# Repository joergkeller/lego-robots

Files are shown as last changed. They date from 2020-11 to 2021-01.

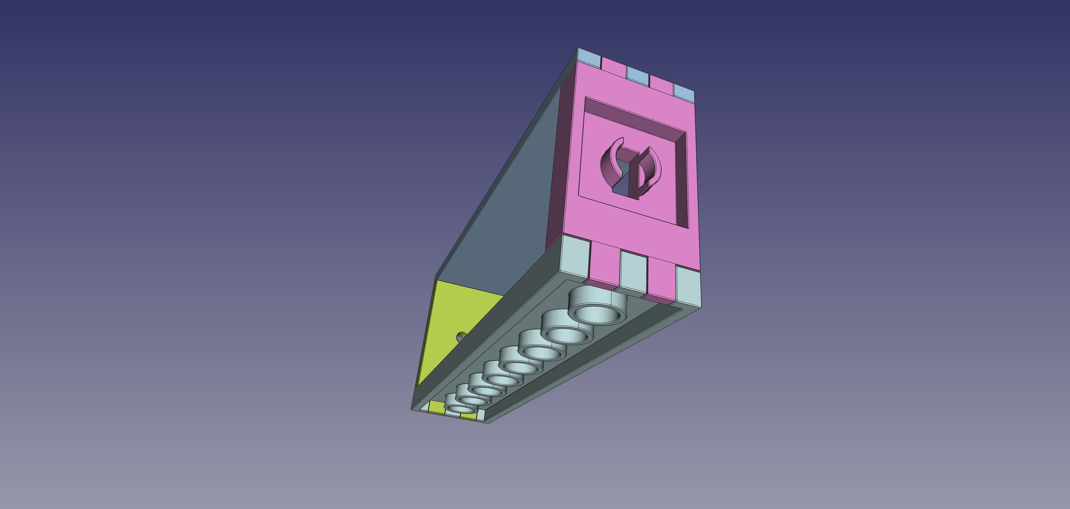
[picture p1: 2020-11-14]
3dp/gearbox-tt-motor/images/motor-case-bottom.png

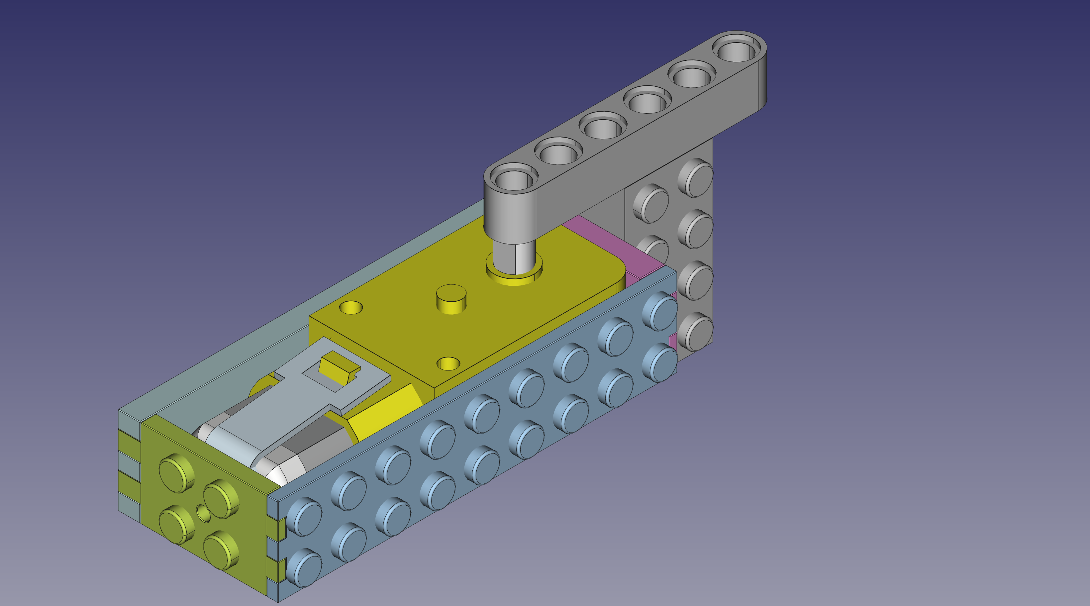
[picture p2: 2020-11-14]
3dp/gearbox-tt-motor/images/motor-case-technic.png

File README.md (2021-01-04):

# Lego Roboter
Adapter-Platten und Code für Lego Roboter mit Arduino.

## 3D-Prints
* Lego-Adapter für Gearbox TT DC Motor
* Case für Sparkfun Qwiik Motor Driver

## Control Code
* Control 2 motors with Joystick using Adafruit QT Py (M0)

# Ideen

## Controller
* [Metro ESP32-S2](https://www.adafruit.com/product/4775): ESP32-S2, Uno, Qwiic, LiPo, max. 12V Input
* [TTGO T7 Mini32](http://www.lilygo.cn/prod_view.aspx?TypeId=50033&Id=978&FId=t3:50033:3): ESP32, Qwiic, LiPo, 
* [Beetle ESP32](https://www.dfrobot.com/product-1798.html): ESP32, 4x Digital, 4x Analog, I2C, 5V Input
* [QT Py](https://www.adafruit.com/product/4600): M0, Qwiic, 5V Input

## Motor Driver
* [Qwiic Motor Driver](https://www.sparkfun.com/products/15451): 2x DC Motor, I2C, 6-12V, 1.2-1.5A
* [Arduino Motor/Stepper/Servo Shield](https://www.adafruit.com/product/1438): 4x Motor oder 2x Stepper, 2x Servo, I2C, 4.5-13.5V, 1.2-2.0A
* [Motor/Stepper Feather Wing](https://www.adafruit.com/product/2927): 4x Motor oder 2x Stepper, I2C, 4.5-13.5V, 1.2A

## Proximity
* [Qwiic Proximity/Gesture/Light/RGB](https://www.adafruit.com/product/3595)

## Joystick
* [Analog ohne Switch](https://www.adafruit.com/product/444): 19x19x9 mm
* [Analog mit Switch](https://www.adafruit.com/product/512): 38x38x32 mm
* [Analog mit Switch](https://www.sparkfun.com/products/9032): 26x32x35 mm
* [I2C, Analog mit Switch](https://www.sparkfun.com/products/15168)

## Diverses
* [Qwiic Differential I2C](https://www.sparkfun.com/products/14589): z.B. Kabelfernsteuerung
* [Qwiic Rotary Encoder](https://www.sparkfun.com/products/15083)
* [I2C Port Expander In/Out, Key driver](https://www.sparkfun.com/products/13601)

Further
* https://maker.pro/arduino/projects/how-to-control-an-arduino-robot-with-a-ps4-bluetooth-controller
* https://techtutorialsx.com/2020/02/16/esp32-connecting-a-ps3-controller/

# Bestellungen

| Komponente | Nr. | Bastelgarage | Mouser | Digikey |
| --- | --- | --- | --- | --- |
| Qwiic Motor Driver | ROB-15451 | - | 15.- [474-ROB-15451](https://www.mouser.ch/ProductDetail/474-ROB-15451) | 14.- [ROB-15451](https://www.digikey.ch/products/de?keywords=ROB-15451) | 
| Qwiic Joystick | COM-15168 | - | - | 9.- [COM-15168](https://www.digikey.ch/products/de?keywords=COM-15168)
| Qwiic Cable 100mm | [4210](https://www.adafruit.com/product/4210) | | | 0.85 [1528-4210-ND](https://www.digikey.ch/product-detail/de/4210/1528-4210-ND/10230021/?itemSeq=347876058)
| Beetle ESP32 (Mini) | [SKU:DFR0575](https://www.dfrobot.com/product-1798.html) | 17.- [Beetle ESP32](https://www.bastelgarage.ch/beetle-esp32-mikrocontroller) | 13.- [426-DFR0575](https://www.mouser.de/ProductDetail/DFRobot/DFR0575?qs=0lSvoLzn4L%252Bs0iCsotbjvQ%3D%3D) | (15.- [DFR0575-ND](https://www.digikey.com/en/products/detail/dfrobot/DFR0575/9805793?s=N4IgTCBcDaICIDEBKAGArAdjSAugXyA)) |
| TTGO T7 Mini32 v1.4 | [T7 Mini32](http://www.lilygo.cn/prod_view.aspx?TypeId=50033&Id=978&FId=t3:50033:3) ($10) | - | - | - | 
| Adafruit QT Py | [4600](https://www.adafruit.com/product/4600) | - | (6.- [485-4600](https://www.mouser.ch/ProductDetail/Adafruit/4600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)) | (6.- [1528-4600-ND](https://www.digikey.ch/products/de?keywords=adafruit%204600)) |
| Adafruit Feather S2 | [4769](https://www.adafruit.com/product/4769) | - | (21.- [485-4769](https://www.mouser.ch/ProductDetail/Adafruit/4769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)) | (20.- [1528-4769-ND](https://www.digikey.ch/products/de?keywords=adafruit%204769))  |
| Batteriehalter 4x AA | | | | 1.80 [Snap no switch](https://www.digikey.ch/product-detail/de/mpd-memory-protection-devices/BC4AASF/BC4AASF-ND/2439259)
| Batteriehalter 6x AA | [248](https://www.adafruit.com/product/248) | | 
| Batteriehalter 8x AA | [875](https://www.adafruit.com/product/875) | - | 5.50 [485-875](https://www.mouser.ch/ProductDetail/Adafruit/875?qs=%2Fha2pyFaduizQR4J0KLqUOCJvC8o7PvfVDMcjxi9FxQ%3D) | 5.40 [1528-1165-ND](https://www.digikey.ch/product-detail/de/adafruit-industries-llc/875/1528-1165-ND/5353625) <br/> 2.70 [Snap no switch](https://www.digikey.ch/product-detail/de/mpd-memory-protection-devices/BH48AASF/BH48AASF-ND/1951883)
| DC-Jack 2.1/5.5mm | | | 1.- [163-1060-EX](https://www.mouser.ch/ProductDetail/Kobiconn/163-1060-EX?qs=%2Fha2pyFaduiKOJdLWmEw0r8MjDVUk%2FgXSdyB8vAjlO0%3D) | 1.50 [486-3380-ND](https://www.digikey.ch/product-detail/de/schurter-inc/4840-2200/486-3380-ND/1212406)
| Pushbutton |
| 2x Sparkfun Joystick | [COM-09032](https://www.sparkfun.com/products/9032) | | 3.60 [474-COM-09032](https://www.mouser.ch/ProductDetail/SparkFun/COM-09032?qs=WyAARYrbSnb9u7eU4VaEfQ%3D%3D) | 3.60 [1568-1526-ND](https://www.digikey.ch/product-detail/de/sparkfun-electronics/COM-09032/1568-1526-ND/6823623)
| Rotary Encoder/Switch | | | | 3.20 [6mm abgeflacht](https://www.digikey.ch/product-detail/de/cui-devices/ACZ11BR4E-15FD1-20C/102-1769-ND/1923364)
| 2x Multihub Wheel | [4205](https://www.adafruit.com/product/4205)| | | 1.95 [1528-2964-ND](https://www.digikey.ch/products/de?keywords=adafruit%204205)
| Gearmotor 105rpm 6V | [FIT0484](https://www.dfrobot.com/product-1434.html) | | | 11.- [FIT0484](https://www.digikey.ch/product-detail/de/dfrobot/FIT0484/1738-1264-ND/7087161)

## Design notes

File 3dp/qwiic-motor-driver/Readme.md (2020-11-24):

# I2C-gesteuerter Motor Treiber

[Sparkfun Qwiic Motor Driver](https://www.sparkfun.com/products/15451)
* 2x DC Motor
* I2C (Qwiic)
* 3.3V VCC und Logik, 6-12V, 1.2A steady state, max. 1.5A pro Kanal

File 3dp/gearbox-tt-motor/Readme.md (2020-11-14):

# Gearbox TT DC Motor

https://www.bastelgarage.ch/bauteile/stepper-motoren/dc-motoren/getriebemotor-1-48

https://www.adafruit.com/product/3777

## 3D-Print Adapter
Die 4 Lego-Adapter können jeweils passend angeordnet gedruckt werden. Meine beiden Prototypen wurden mit ABS gedruckt, 0.2 mm Düse, 0.1 mm Layer, Nachbearbeitung mit Feile und Drahtbürste.

Die 4 Teile wurden bündig um den Motor eingepasst, der Nippel beim Getriebe und die Achse beim Motor passen bündig in die Stirnseiten, die beiden anderen Teile können verzahnt verbunden werden (evtl. mit Schleifpapier nachbessern). Mit Weissleim oder Sekundenkleber verkleben. Ich habe mit Legosteinen einen Halter gebaut um die richtige Ausrichtung beim Trocknen sicherzustellen.

## Technische Details
* Betriebsspannung: 3V bis 6V DC
* Stromaufnahme: max ca. 250mA
* Torque: max. 0.8kg/cm
* Getriebe Verhältnis: 1:48
* Geschwindigkeit: ca. 26 RPM bei 3V, 44RPM bei 5V
* Abmessung: 69 x 22.5 x 36.5mm
* Gewicht: 27g

## 3D-Model
https://grabcad.com/library/dc-3v-6v-tt-motor-1

## Zubehör
* [68 mm Rad](https://www.adafruit.com/product/3763)
* [65 mm Lego-Rad mit Adapter](https://www.adafruit.com/product/4205)
* [Lego-Adapter](https://www.adafruit.com/product/3810)
* [Adapter](https://www.adafruit.com/product/3769)
* [Encoder-Scheibe](https://www.adafruit.com/product/3782)

## Alternative
* [TT-Motor Metall](https://www.adafruit.com/product/3801)
* [TT-Motor mit Encoder](https://www.sparkfun.com/products/16413)
* [N20 Motor mit Encoder](https://www.adafruit.com/product/4639)
* [Mini Stepper Motor](https://www.adafruit.com/product/4411)

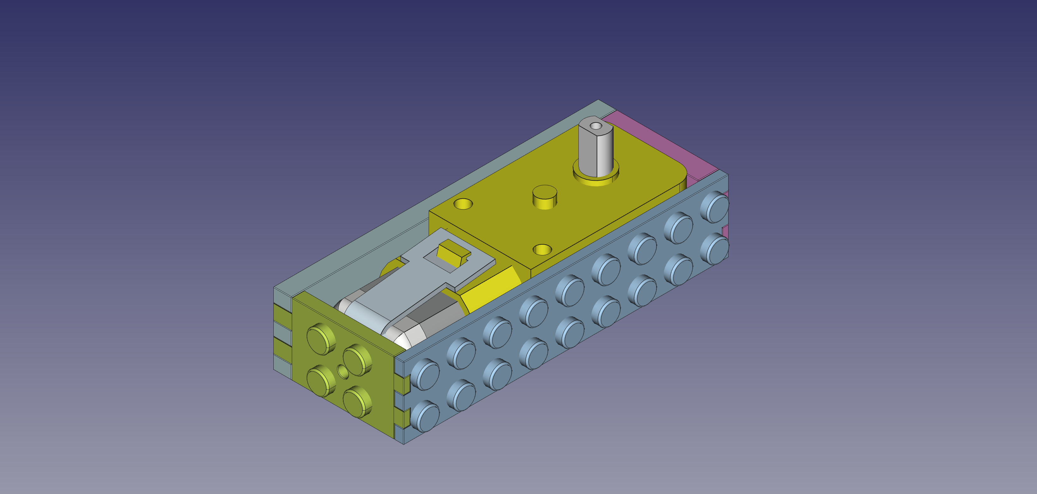
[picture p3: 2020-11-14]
3dp/gearbox-tt-motor/images/motor-case-with-gearbox-tt.png

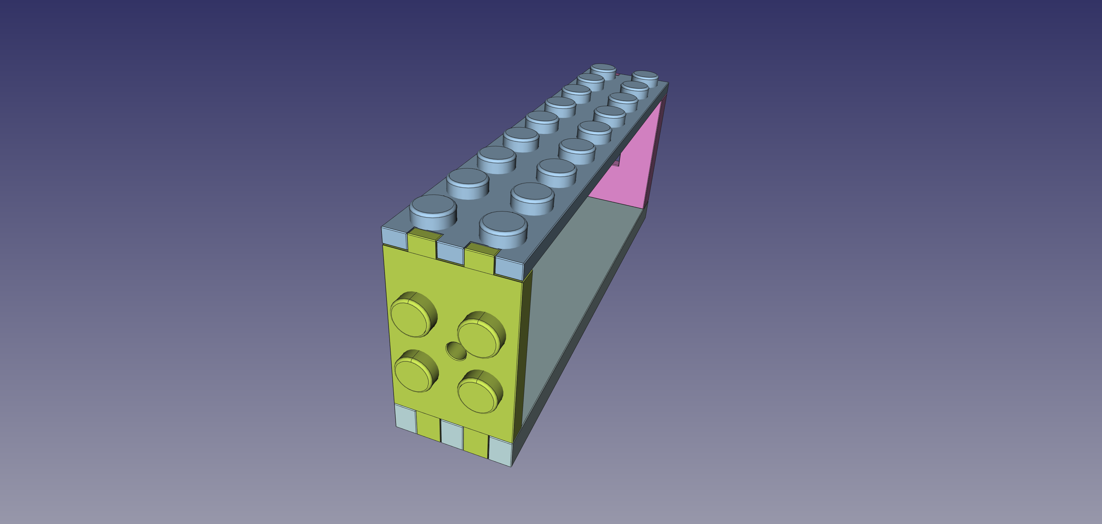
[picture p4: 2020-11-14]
3dp/gearbox-tt-motor/images/motor-case-top.png

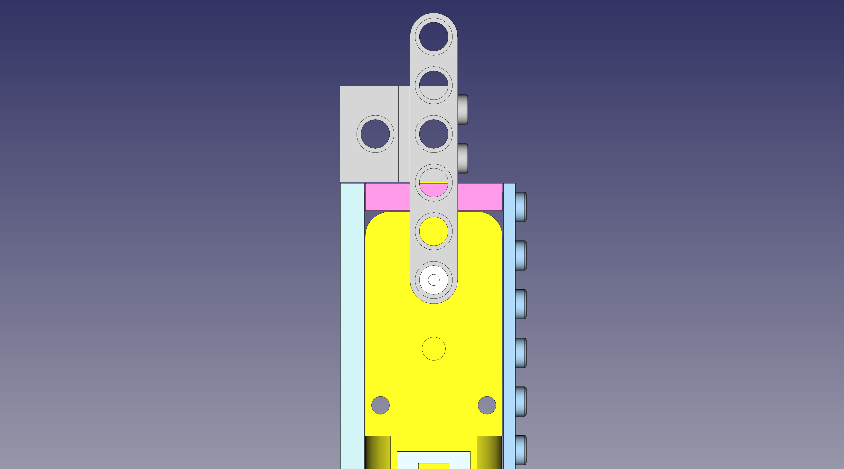
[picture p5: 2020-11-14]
3dp/gearbox-tt-motor/images/motor-case-technic-aligned.png

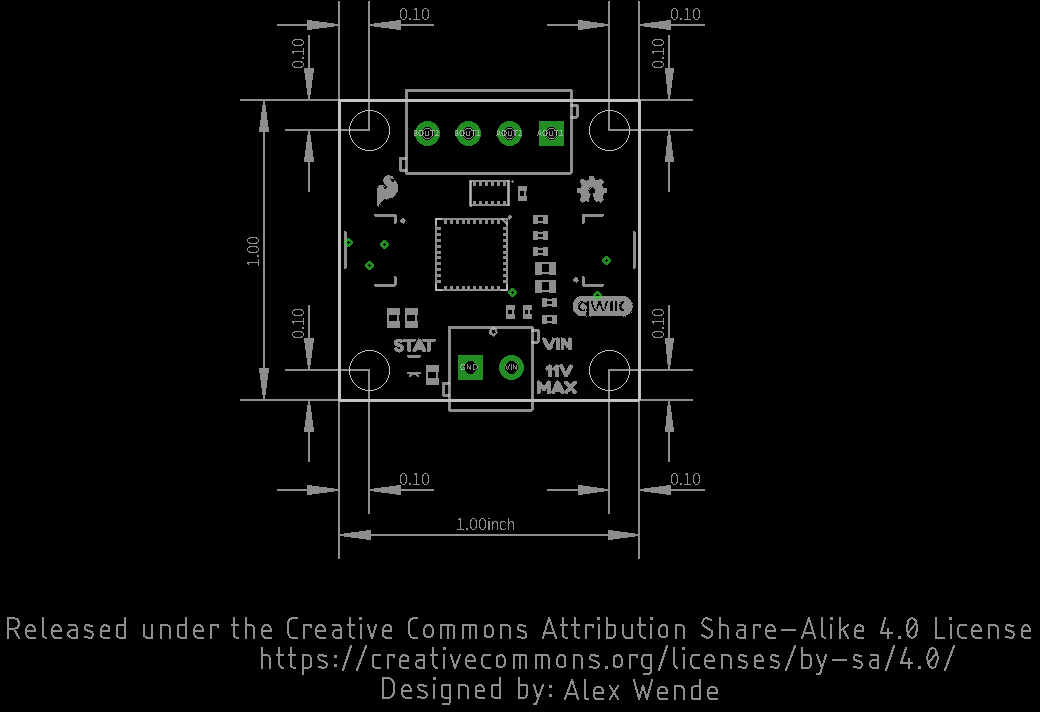
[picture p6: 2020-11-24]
3dp/qwiic-motor-driver/images/Qwiic_Motor_driver_Dimensions.png

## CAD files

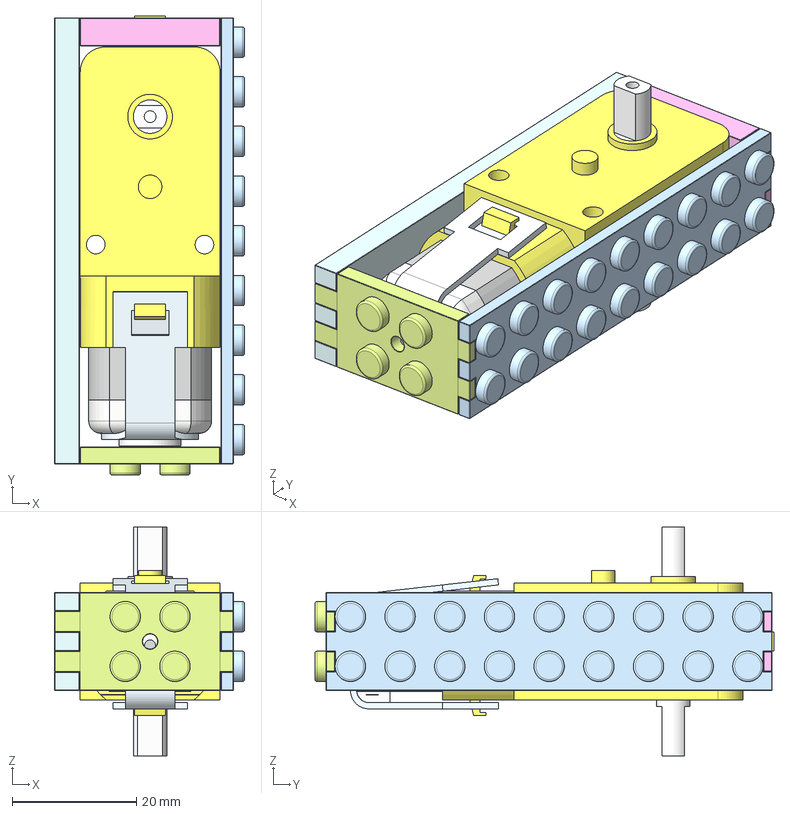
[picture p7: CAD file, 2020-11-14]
3dp/gearbox-tt-motor/Motor Case.FCStd
30.6 x 73.9 x 36.8 mm
Surface 1
M
Top Plate
Gear Plate
Motor Plate
Bottom Plate

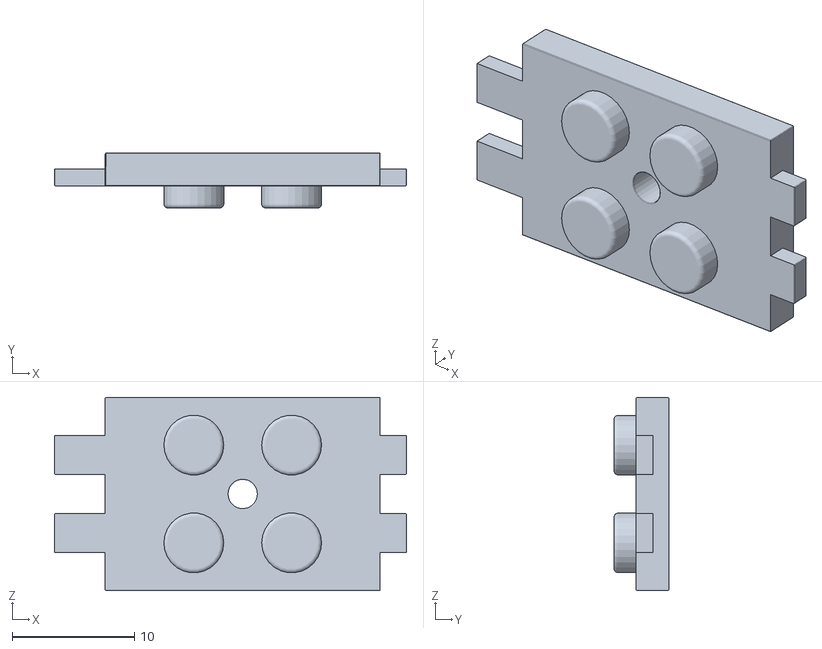
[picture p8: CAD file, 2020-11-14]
3dp/gearbox-tt-motor/prints/motor-case-motor.stl
28.8 x 4.50 x 15.8

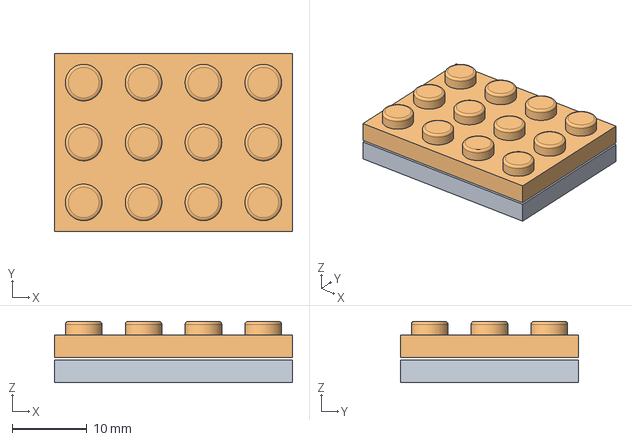
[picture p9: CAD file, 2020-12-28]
3dp/lego/Generic Plates.FCStd
31.8 x 23.8 x 8.20 mm
Base Plate
Top Plate

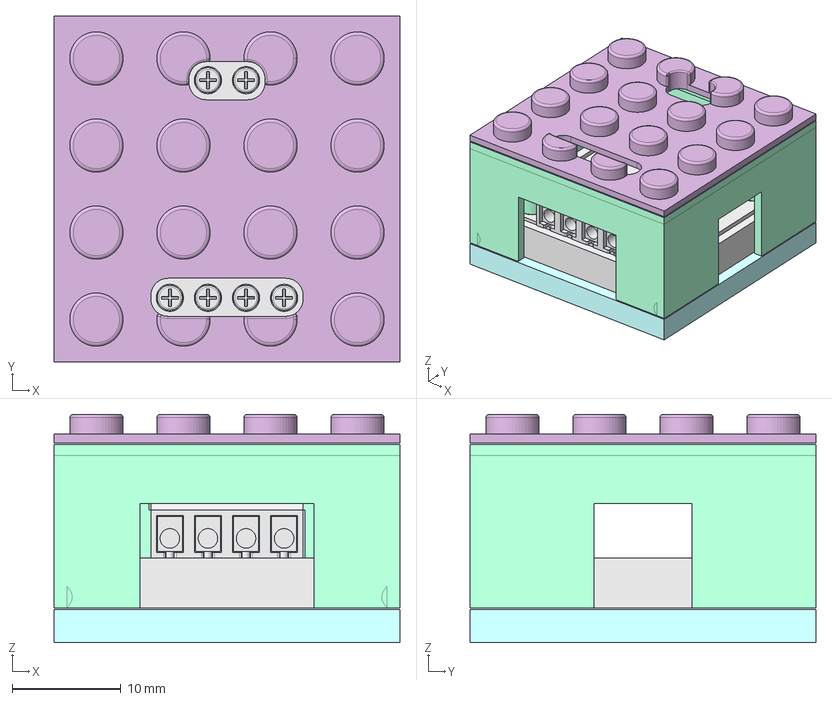
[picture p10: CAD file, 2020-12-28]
3dp/qwiic-motor-driver/Driver Case.FCStd
31.8 x 31.8 x 21.0 mm
PCB
Vin
Motor
Cover
Noppen
Bottom
Base

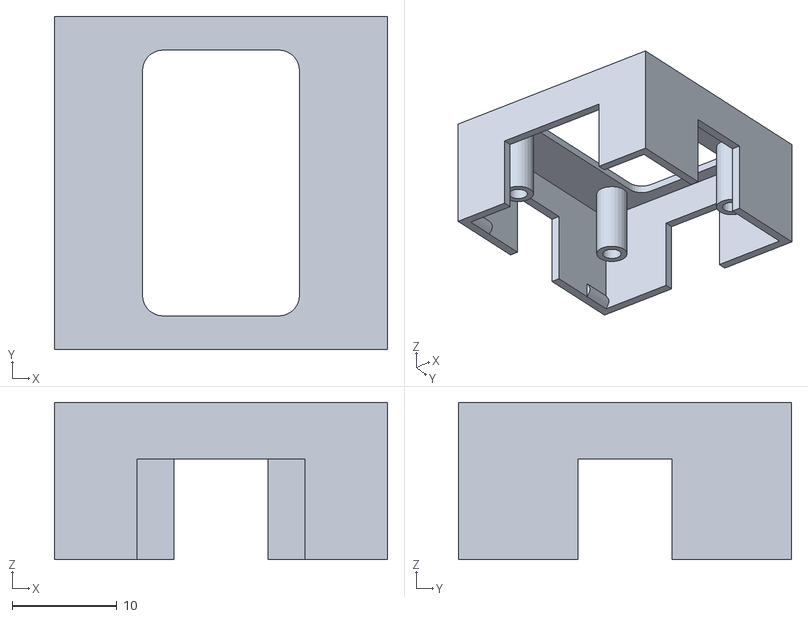
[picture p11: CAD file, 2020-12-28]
3dp/qwiic-motor-driver/prints/Driver Case Cover.stl
31.8 x 31.8 x 15.0

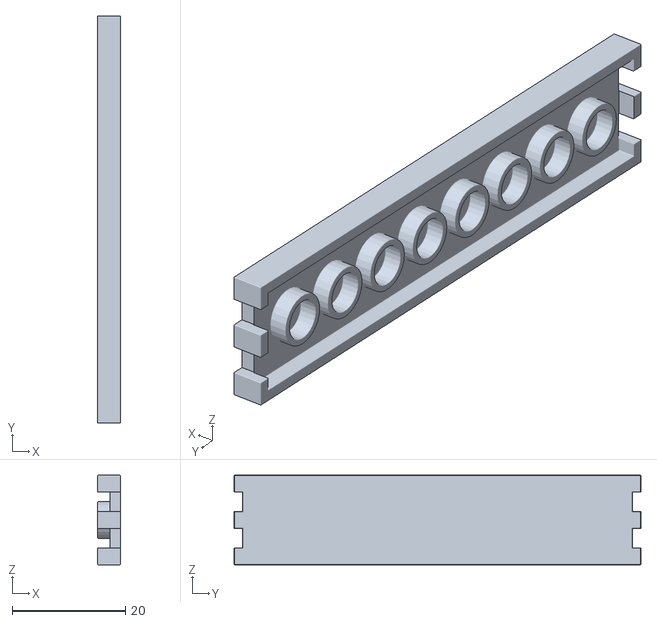
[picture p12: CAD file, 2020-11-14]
3dp/gearbox-tt-motor/prints/motor-case-bottom.stl
4.00 x 71.8 x 15.8

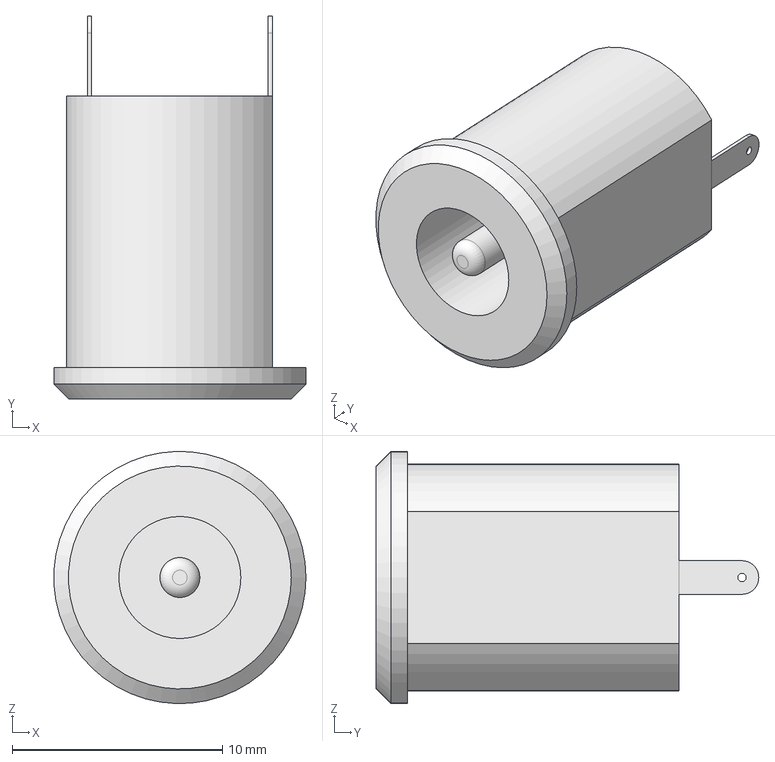
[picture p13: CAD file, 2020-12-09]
3dp/qwiic-motor-driver/DC Power Jack.FCStd
12.0 x 18.2 x 12.0 mm

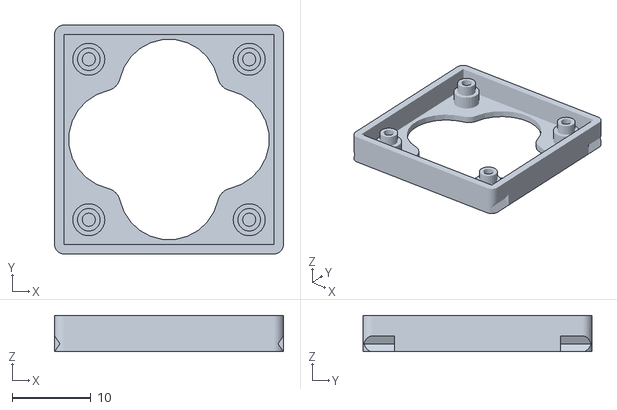
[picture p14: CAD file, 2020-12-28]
3dp/qwiic-motor-driver/prints/Driver Case Bottom.stl
29.0 x 29.0 x 4.60

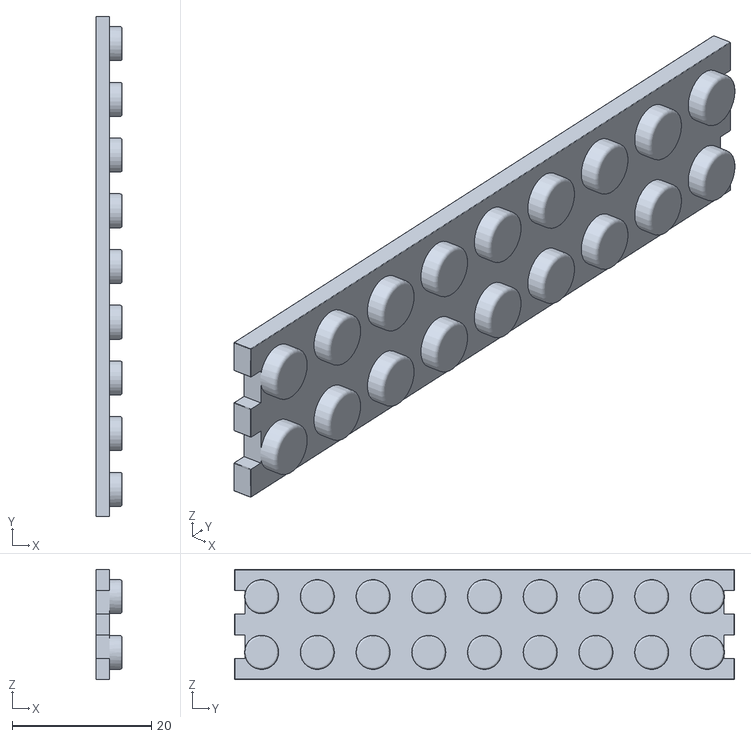
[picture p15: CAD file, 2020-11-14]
3dp/gearbox-tt-motor/prints/motor-case-top.stl
3.80 x 71.8 x 15.8

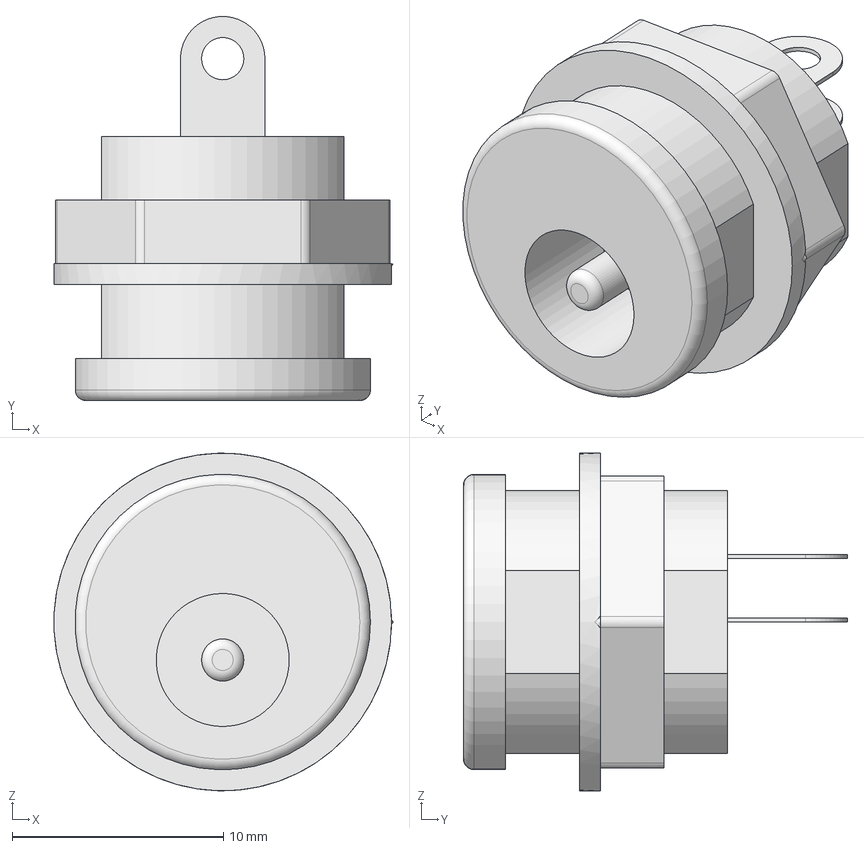
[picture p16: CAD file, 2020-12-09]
3dp/qwiic-motor-driver/DC Power Jack geschraubt.FCStd
16.1 x 18.2 x 16.0 mm

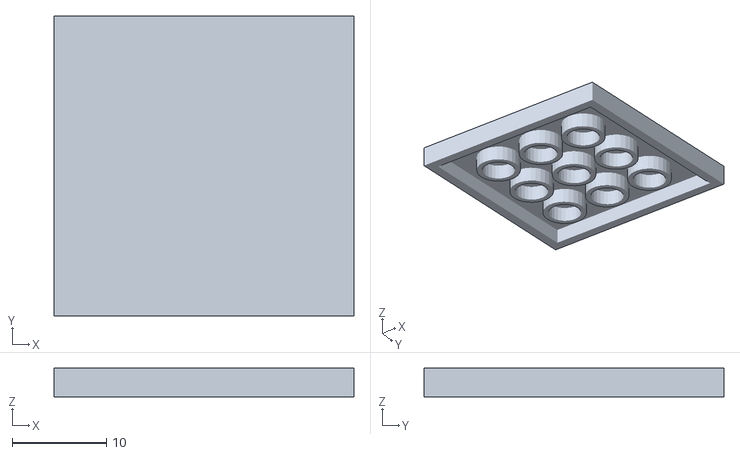
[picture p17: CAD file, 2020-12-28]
3dp/qwiic-motor-driver/prints/Driver Case Base.stl
31.8 x 31.8 x 3.05

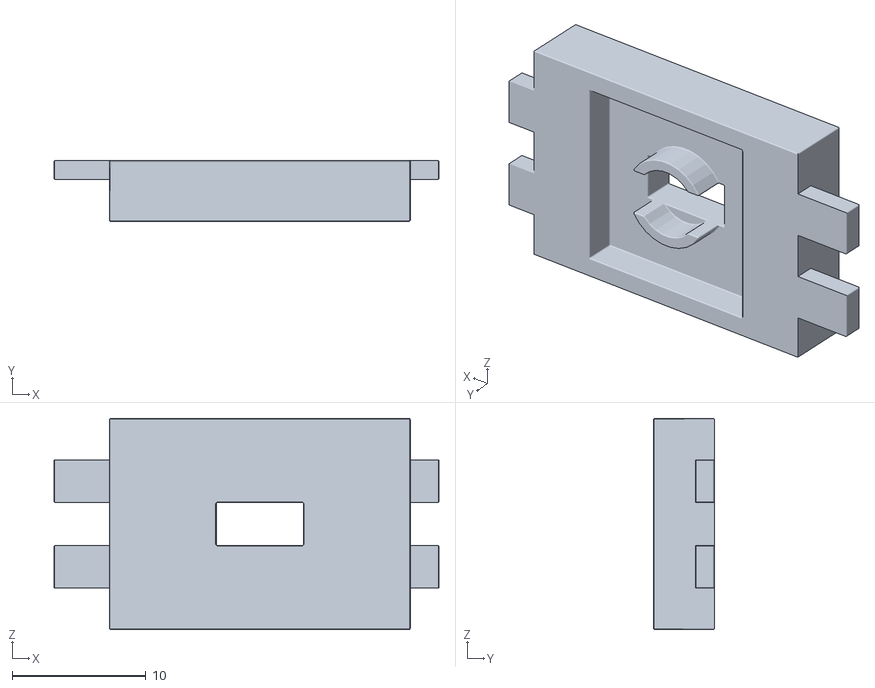
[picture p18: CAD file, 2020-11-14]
3dp/gearbox-tt-motor/prints/motor-case-gear.stl
28.8 x 4.55 x 15.8

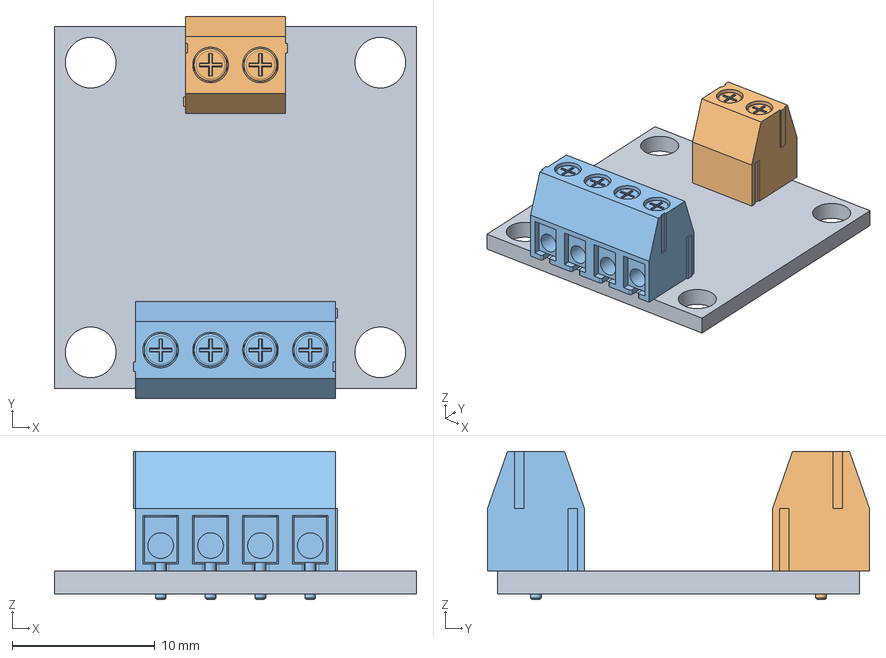
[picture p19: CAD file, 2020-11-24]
3dp/qwiic-motor-driver/Motor Driver.FCStd
25.4 x 26.8 x 10.4 mm
PCB
Vin
Motor

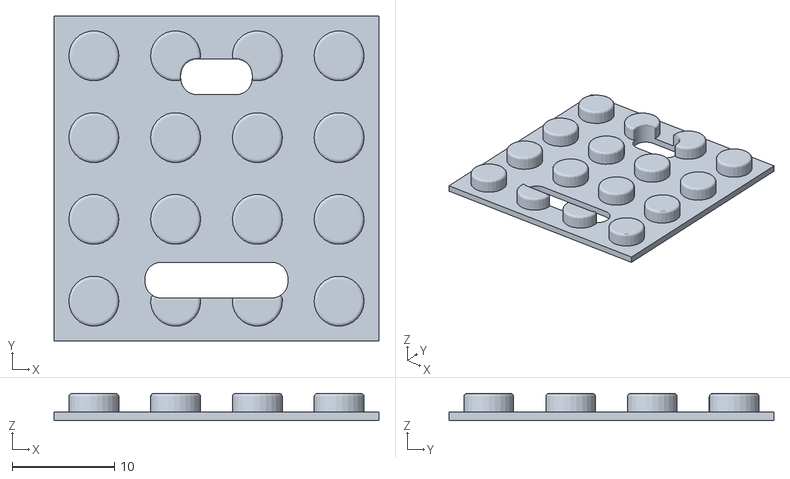
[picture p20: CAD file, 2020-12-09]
3dp/qwiic-motor-driver/prints/Driver Case Noppen.stl
31.8 x 31.8 x 2.65

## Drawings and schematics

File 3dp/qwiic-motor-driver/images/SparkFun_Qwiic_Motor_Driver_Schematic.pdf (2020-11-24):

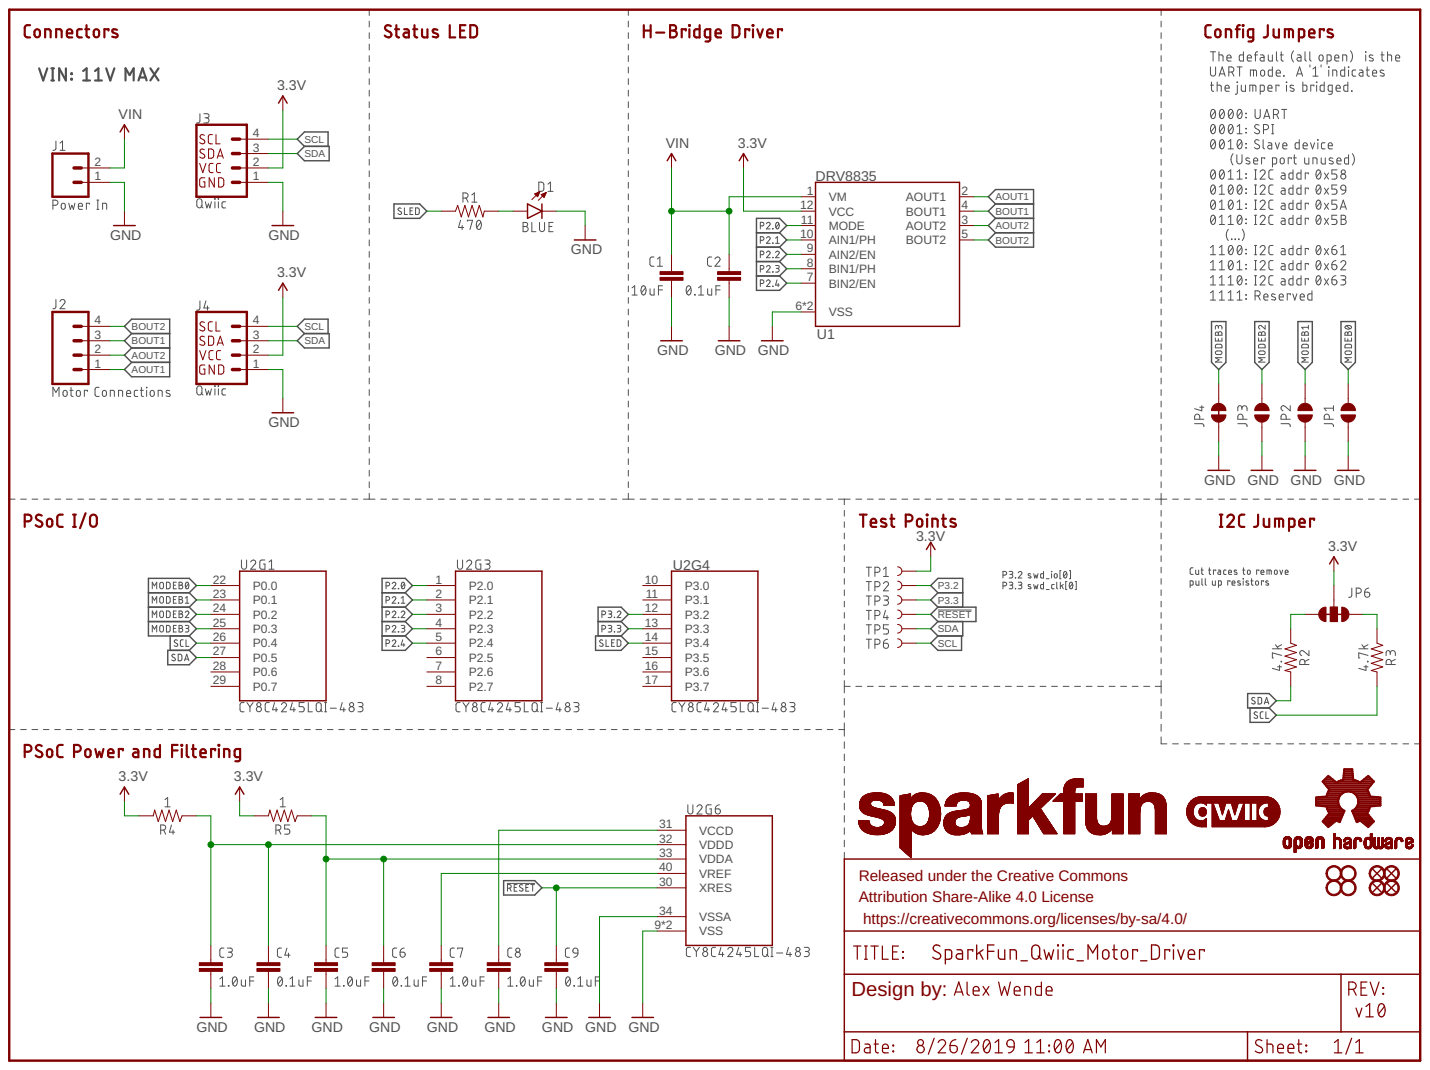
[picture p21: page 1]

GND GND

Released under the Creative Commons Attribution Share-Alike 4.0 License

https://creativecommons.org/licenses/by-sa/4.0/

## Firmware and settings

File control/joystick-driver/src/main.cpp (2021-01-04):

#include <Arduino.h>
#include <Adafruit_NeoPixel.h>
#include "SparkFun_Qwiic_Joystick_Arduino_Library.h" 
#include "SCMD.h"
#include "SCMD_config.h" //Contains #defines for common SCMD register names and values
#include "Wire.h"

#define X_CENTER   524
#define Y_CENTER   513

#define NEO_PIN     11
#define NUM_PIXELS   1

#define DIRECTION_ATTENUATION   3
#define MAX_SPEED             150
#define MAX_SPEED_CHANGE        5
#define CHANGE_INTERVAL        50 // ms

#define LEFT_MOTOR 0
#define RIGHT_MOTOR 1

// I2C controlled analog Joystick with button
JOYSTICK joystick; 

// When setting up the NeoPixel library, we tell it how many pixels,
// and which pin to use to send signals. Note that for older NeoPixel
// strips you might need to change the third parameter -- see the
// strandtest example for more information on possible values.
Adafruit_NeoPixel pixels(NUM_PIXELS, NEO_PIN, NEO_GRB + NEO_KHZ800);

// This creates the main object of one motor driver and connected peripherals
SCMD myMotorDriver; 

int16_t oldVector = 0;
int16_t oldOffset = 0;


void setup() {
  Serial.begin(115200);
  Serial.println("Qwiic Joystick Motor Driver");

  // Initialize joystick
  while(joystick.begin() == false) {
    Serial.println("Joystick does not appear to be connected. Please check wiring...");
  }

  // Initialize neo-pixel
  pixels.begin(); 
  pixels.setBrightness(128);

  // Initialize motor driver
  myMotorDriver.settings.commInterface = I2C_MODE;
  myMotorDriver.settings.I2CAddress = 0x5D; //config pattern is "1000" (default) on board for address 0x5D

  while (myMotorDriver.begin() != 0xA9) { //Wait until a valid ID word is returned
    Serial.println( "ID mismatch, trying again" );
    delay(500);
  }
  Serial.println( "ID matches 0xA9" );

  // Check to make sure the driver is done looking for peripherals before beginning
  Serial.print("Waiting for enumeration...");
  while ( myMotorDriver.ready() == false );
  Serial.println("Done.");
  Serial.println();

  // Set motor inversion (so for both motors 'forward' means the same thing)
  while ( myMotorDriver.busy() ); //Waits until the SCMD is available.
  myMotorDriver.inversionMode(LEFT_MOTOR, 0);
  myMotorDriver.inversionMode(RIGHT_MOTOR, 0);

  // Enables the output driver hardware
  while ( myMotorDriver.busy() );
  myMotorDriver.enable(); 
}

void loop() {
  // Get joystick state
  int x = joystick.getHorizontal();
  Serial.print("X: ");
  Serial.print(x);

  int y = joystick.getVertical();
  Serial.print(" Y: ");
  Serial.print(y);
  
  byte button = joystick.getButton();
  Serial.print(" Button: ");
  Serial.print(button);

  // Normalize joystick position, considering center position
  uint16_t forward = map(max(0, y - Y_CENTER), 0, 1023-Y_CENTER, 0, 255);
  Serial.print(" Forward: ");
  Serial.print(forward);
  uint16_t backward = map(-min(0, y - Y_CENTER), 0, Y_CENTER, 0, 255);
  Serial.print(" Backward: ");
  Serial.print(backward);

  uint16_t left = map(max(0, x - X_CENTER), 0, 1023-X_CENTER, 0, 255);
  Serial.print(" Left: ");
  Serial.print(left);
  uint16_t right = map(-min(0, x - X_CENTER), 0, X_CENTER, 0, 255);
  Serial.print(" Right: ");
  Serial.print(right);

  // Show direction in pixel color
  uint8_t red = backward;
  uint8_t green = left + right;
  uint8_t blue = forward;
  pixels.setPixelColor(0, pixels.Color(red, green, blue));
  pixels.show();

  // Limit acceleration and speed
  int16_t moveVector = ((int16_t)forward) - backward;
  int16_t directionOffset = (((int16_t)left) - right) / DIRECTION_ATTENUATION;
  if ((moveVector - oldVector) > MAX_SPEED_CHANGE) {
    moveVector = min(oldVector + MAX_SPEED_CHANGE, MAX_SPEED);
  } else if ((moveVector - oldVector) < -MAX_SPEED_CHANGE) {
    moveVector = max(oldVector - MAX_SPEED_CHANGE, -MAX_SPEED);
  }
  oldVector = moveVector;

  // Drive motor
  int16_t moveLeft = moveVector + directionOffset;
  int16_t moveRight = moveVector - directionOffset;
  Serial.print(" Move left: "); 
  Serial.print(moveLeft);
  Serial.print(" Move right: "); 
  Serial.print(moveRight);
  while ( myMotorDriver.busy() ); //Waits until the SCMD is available.
  if (moveLeft >= 0) {
    uint8_t level = min(moveLeft, 255);
    myMotorDriver.setDrive(LEFT_MOTOR, 0, level);
  } else {
    uint8_t level = min(-moveLeft, 255);
    myMotorDriver.setDrive(LEFT_MOTOR, 1, level);
  }
  if (moveRight >= 0) {
    uint8_t level = min(moveRight, 255);
    myMotorDriver.setDrive(RIGHT_MOTOR, 0, level);
  } else {
    uint8_t level = min(-moveRight, 255);
    myMotorDriver.setDrive(RIGHT_MOTOR, 1, level);
  }

  Serial.println();
  delay(CHANGE_INTERVAL);
}

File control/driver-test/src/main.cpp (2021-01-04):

//This example drives a robot in left and right arcs, driving in an overall wiggly course.
//  It demonstrates the variable control abilities. When used with a RedBot chassis,
//  each turn is about 90 degrees per drive.
//
//  Pin 8 can be grounded to disable motor movement, for debugging.

#include <Arduino.h>
#include <stdint.h>
#include "SCMD.h"
#include "SCMD_config.h" //Contains #defines for common SCMD register names and values
#include "Wire.h"

#define LEFT_MOTOR 0
#define RIGHT_MOTOR 1

#define STEP_DURATION 10

SCMD myMotorDriver; //This creates the main object of one motor driver and connected peripherals.

void setup()
{
  pinMode(8, INPUT_PULLUP); //Use to halt motor movement (ground)

  Serial.begin(9600);
  delay(5000);
  Serial.println("Starting sketch.");

  //***** Configure the Motor Driver's Settings *****//
  //  .commInter face is I2C_MODE 
  myMotorDriver.settings.commInterface = I2C_MODE;

  //  set address if I2C configuration selected with the config jumpers
  myMotorDriver.settings.I2CAddress = 0x5D; //config pattern is "1000" (default) on board for address 0x5D

  //  set chip select if SPI selected with the config jumpers
  myMotorDriver.settings.chipSelectPin = 10;

  //*****initialize the driver get wait for idle*****//
  while ( myMotorDriver.begin() != 0xA9 ) //Wait until a valid ID word is returned
  {
    Serial.println( "ID mismatch, trying again" );
    delay(500);
  }
  Serial.println( "ID matches 0xA9" );

  //  Check to make sure the driver is done looking for peripherals before beginning
  Serial.print("Waiting for enumeration...");
  while ( myMotorDriver.ready() == false );
  Serial.println("Done.");
  Serial.println();

  //*****Set application settings and enable driver*****//

  //Uncomment code for motor 0 inversion
  //while( myMotorDriver.busy() );
  //myMotorDriver.inversionMode(0, 1); //invert motor 0

  //Uncomment code for motor 1 inversion
  while ( myMotorDriver.busy() ); //Waits until the SCMD is available.
  myMotorDriver.inversionMode(LEFT_MOTOR, 0);  // don't invert motor
  myMotorDriver.inversionMode(RIGHT_MOTOR, 0); // don't invert motor

  while ( myMotorDriver.busy() );
  myMotorDriver.enable(); //Enables the output driver hardware
}

void loop()
{
  //pass setDrive() a motor number, direction as 0 (call 0 forward) or 1, and level from 0 to 255
  myMotorDriver.setDrive( LEFT_MOTOR, 0, 0); //Stop motor
  myMotorDriver.setDrive( RIGHT_MOTOR, 0, 0); //Stop motor
  while (digitalRead(8) == 0); //Hold if jumper is placed between pin 8 and ground

  //***** Operate the Motor Driver *****//
  //  This moves both motors up, one faster than the other to drive a circle.
  //  It uses .setDrive( motorNum, direction, level ) to drive the motors.

  for (int reverse = 0; reverse < 2; reverse++) 
  {
    Serial.print("Smoothly move motors up to speed (drive level 0 to 255)...");
    for (int i = 0; i < 256; i++)
    {
      myMotorDriver.setDrive( LEFT_MOTOR, reverse, i);
      myMotorDriver.setDrive( RIGHT_MOTOR, reverse, 20 + (i / 2));
      delay(STEP_DURATION);
    }
    Serial.println(" and back");
    for (int i = 255; i >= 0; i--)
    {
      myMotorDriver.setDrive( LEFT_MOTOR, reverse, i);
      myMotorDriver.setDrive( RIGHT_MOTOR, reverse, 20 + (i / 2));
      delay(STEP_DURATION);
    }
    Serial.print("Smoothly move motors up to speed...");
    for (int i = 0; i < 256; i++)
    {
      myMotorDriver.setDrive( LEFT_MOTOR, reverse, 20 + (i / 2));
      myMotorDriver.setDrive( RIGHT_MOTOR, reverse, i);
      delay(STEP_DURATION);
    }
    Serial.println(" and back");
    for (int i = 255; i >= 0; i--)
    {
      myMotorDriver.setDrive( LEFT_MOTOR, reverse, 20 + (i / 2));
      myMotorDriver.setDrive( RIGHT_MOTOR, reverse, i);
      delay(STEP_DURATION);
    }
  }
}

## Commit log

2020-11-14 first adapter for tt motor
    [Motor Case.FCStd, motor-case-bottom.stl, motor-case-gear.stl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]
2020-11-14 leaving motor axis aligned instead of offset 0.65mm
    [Motor Case.FCStd, motor-case-motor.stl]
2020-11-24 separate motor driver case
    [Driver Case.FCStd, Motor Driver.FCStd]
2020-11-24 case with snap
    [Driver Case.FCStd]
2020-11-25 redesigned reverse case, bottom can be used independently
    [Driver Case.FCStd]
2020-12-09 updated order list, considered dc jack
    [DC Power Jack geschraubt.FCStd, DC Power Jack.FCStd, motor-case-bottom.stl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]
2020-12-09 driver case optimized for 0.4mm nozzle
    [Driver Case Base.stl, Driver Case Bottom.stl, Driver Case Cover.stl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]
2020-12-10 lego wall 1.6, case wall 1.2
    [Driver Case Base.stl, Driver Case.FCStd]
2020-12-28 after first pla print (MakerSpace winBib): lego wall 1.5, rounded bottom, smaller position pads
    [Driver Case Base.stl, Driver Case Bottom.stl, Driver Case Cover.stl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]
2020-12-28 generic plates
    [Generic Plates.FCStd]
2021-01-04 driver test code and first working joystick-driver
